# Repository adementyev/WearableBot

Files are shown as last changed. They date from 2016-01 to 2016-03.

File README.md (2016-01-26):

#Rovables Project 

#Motor Driver V2 (Main robot controller)
The robot controller board contains the necessary components to make functional robot. 
It has a brain of ATmega328p microcontroller, 6-Axis IMU and 2.4GHz wireless board
Also, it can take input from two encoders. 
A extension board can be placed on the top. 

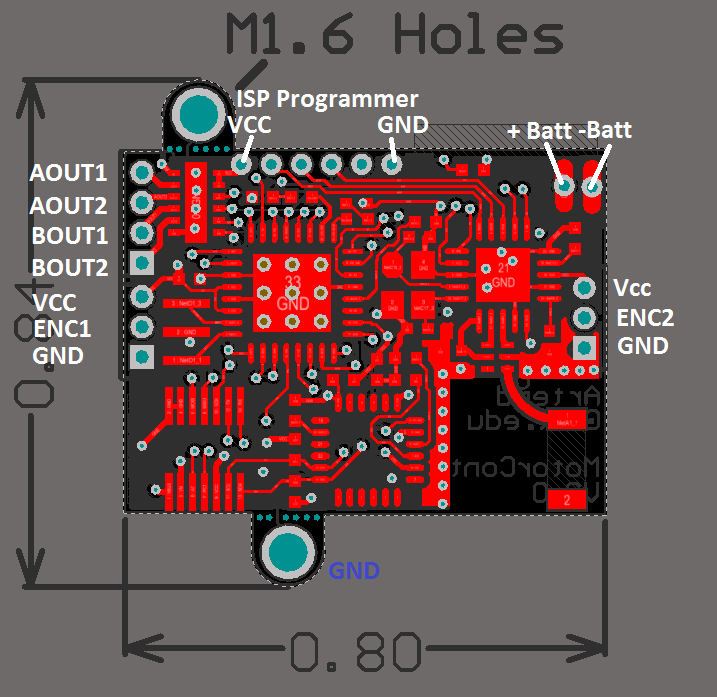
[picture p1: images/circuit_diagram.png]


##Programming the controller board 
The board needs AVRISPmkII programmer, and a special programming adapter. The programming connector can be just pressed fited into the holes. The power is not supplied by the programmer, so a seperate power supply will be needed. 
When programming choose Arduino Pro Mini (3.3V, 8MHz) w/ ATmega328 

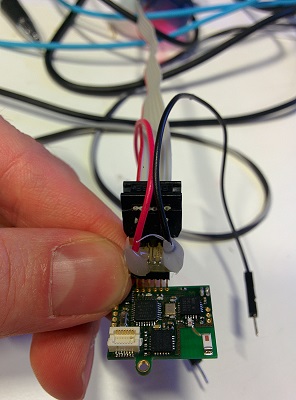
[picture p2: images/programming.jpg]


##Optical Encoders
The board can take two optical encoders. The onboard comparators will convert the analog signals into digital interrupts. Two digital to analog converters (DACs) can be used to set the threshold for comparator. It can be tricky to tune it. It is best done with two oscillascope probes. One on the analog output of optical sensor, and second on the comparator digital output. 

##Problems 
The packet loss is quite large (1 out of 20 ). I suspect it is because of the antenna. 

#Base station board 
Base station allows the robot to wirelessly talk to the computer. 
It is essentially Arduino Leonardo with special connector for a RF dongle. 
The ATMega32u4 processor allow fast USB communications to the computer

##Programming the controller board
The board has a Ardiono USB bootloader so it can be programmed as regular Arduino Leonardo. 

#Software
The current version of the software runs in OpenFrameworks. Tested on Xcode/MacBook Pro only C++ allows for faster 3D graphics, and faster response. The robot can be controlled remotely from the computer.

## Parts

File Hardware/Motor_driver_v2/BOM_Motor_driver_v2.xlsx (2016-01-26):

Comment | Description | Designator | digikey number | Footprint | LibRef | Quantity
ON_OFF_SWITCH | SPDT SMD Side Switch |  | 10 | SWTICH_SMD_SIDE | ON_OFF_SWITCH | 1
2.45 GHz Chip antenna | for Bluetooth | A1 | 712-1005-1-ND | 2450AT18A100E | 2.45 GHz Chip antenna | 1
2.45 GHz Bulan | for nRF8001 chip | B1 | 712-1574-1-ND | 2450BM14A0002 | 2.45 GHz Bulan | 1
100uF 6.3V | Polarised capacitor | C1 | 718-1920-1-ND | CAP1206 | Capacitor_pol | 1
0.1uF | SMD Cap 1206 | C3, C5, C6, C8 | 1276-1443-1-ND | 0402W | Capacitor | 4
10uF 16V | Polarised capacitor | C4 | 478-8654-1-ND | CAP0805 | Capacitor_pol | 1
10nF | SMD Cap 1206 | C7 | 587-3383-1-ND | 0402W | Capacitor | 1
2200pF | SMD Cap 1206 | C9 | 587-3383-1-ND | 0402W | Capacitor | 1
10uF 6.3V | Polarised capacitor | C10 | 478-9265-1-ND | 0805 TANTALUM | Capacitor_pol | 1
0.1uF | SMD Cap 1206 | C11, C12, C14 |  | 0603W | Capacitor | 3
33nF X7R, +/- 10% | SMD Cap 1206 | C13 | 399-4891-1-ND | 0402W | Capacitor | 1
6pF NPO, +/- 2% | SMD Cap 1206 | C15, C17 | 490-8223-1-ND | 0402W | Capacitor | 2
2200pF 5% | SMD Cap 1206 | C16 | 399-8957-1-ND | 0402W | Capacitor | 1
LED RED |  | L2 | LNJ247W82RACT-ND | 0402W
LED BLUE |  | L1 | LNJ947W8CRACT-ND | 0402W | LED | 2
8 MHz resonator | Build in caps | O1 | 490-1195-1-ND | Resonator SMD | Resonator SMD | 1
16 MHz Crystal Cl=8pF | For BLE use | O2 | 644-1169-1-ND | 2.5 x 2.0 crystal | 16 MHz Crystal Wireless | 1
MHDR1X3 | Header, 3-Pin | P1, P2 |  | MHDR1X3 | MHDR1X3 | 2
CONN HEADER 14POS 3MM SMD 0.5MM |  | P3 | H11701CT-ND | DF12 14Pos | CONN HEADER 14POS 3MM SMD 0.5MM | 1
MHDR1X4 | Header, 4-Pin | P4 |  | MHDR1X4 | MHDR1X4 | 1
6 pin smd 1.27mm female |  | P6 | ED90490-ND | 6pos 1.27mm | 6 pin smd 1.27mm female | 1
0 Ohm |  | R1 | 311-0.0GRCT-ND | 0603W | Resistor | 1
330 |  | R2, R3 | 311-330JRCT-ND | 0402W | Resistor | 2
4.7k |  | R4, R5, R6 | 311-4.7KJRCT-ND | 0402W | Resistor | 3
10k |  | R7 | 311-10.0KLRCT-ND | 0402W | Resistor | 1
22K 1% |  | R8 | P20.0KLCT-ND | 0402W | Resistor | 1
3.7V REG | DNP | U1 | 576-2770-1-ND | SOT-23-5 | MIC5205_VOLTAGE_REG | 1
MPU 6050 | Gyro / accelerometer combo | U2 |  | QFN24 | MPU_6500 | 1
ATmega328P-MUR | 8-bit AVR Microcontroller, 32KB Flash, 1KB EEPROM, 2KB SRAM, 32-pin MLF, Industrial Grade (-40°C to 85°C) | U3 | ATMEGA328P-MURCT-ND | 32M1-A_M | ATmega328P-MUR | 1
3.3 V REG | 150mA | U4 | 576-1259-1-ND | SOT-23-5 | MIC5205_VOLTAGE_REG | 1
DRV8835 | motor driver | U5 | 296-30391-1-ND | WSON-16 | DRV8835 | 1
MCP4725 | 12bit DAC | U6, U9 | MCP4725A0T-E/CHCT-ND | SOT23-6 | MCP4725 | 2
TS882IST | Rail-to-rail 1.1 V dual comparatpr | U7 | 497-13800-1-ND | MiniS08 | TS882IST | 1
nRF24L01+ | 2.4 GHz Radio | U8 | 1490-1033-1-ND | QFN20 | nRF24L01+ | 1

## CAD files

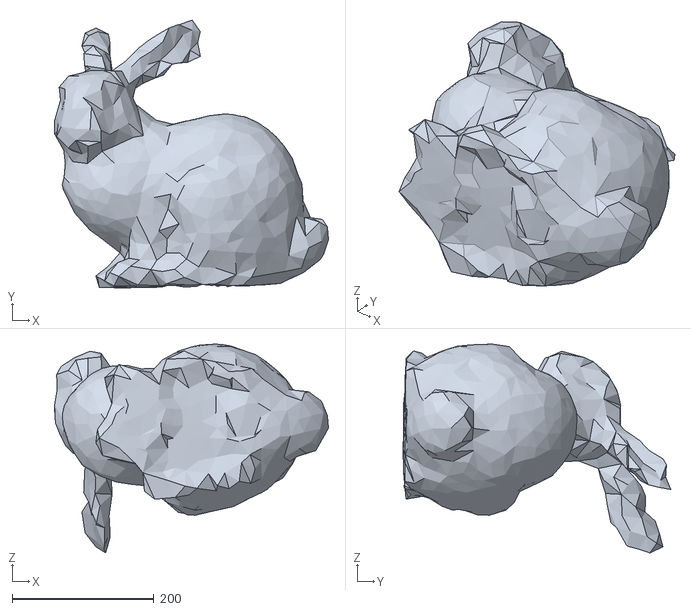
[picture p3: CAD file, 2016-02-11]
Software/onBodyNavigation_V2/bin/data/lofi-bunny_large.ply
386.4 x 377.6 x 294.6

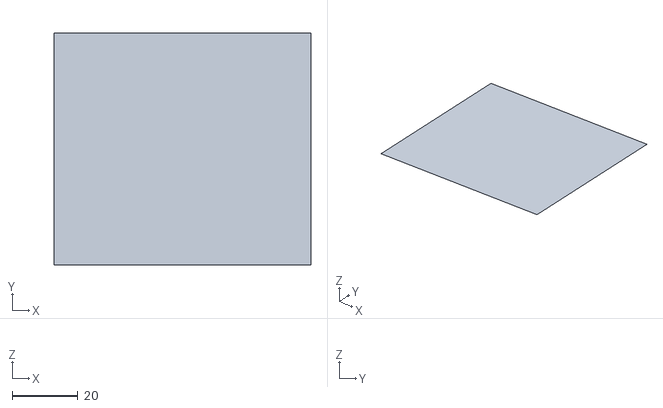
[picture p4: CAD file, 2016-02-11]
Software/onBodyNavigation_V2/bin/data/mesh_try2.ply
78.2 x 70.5 x 0

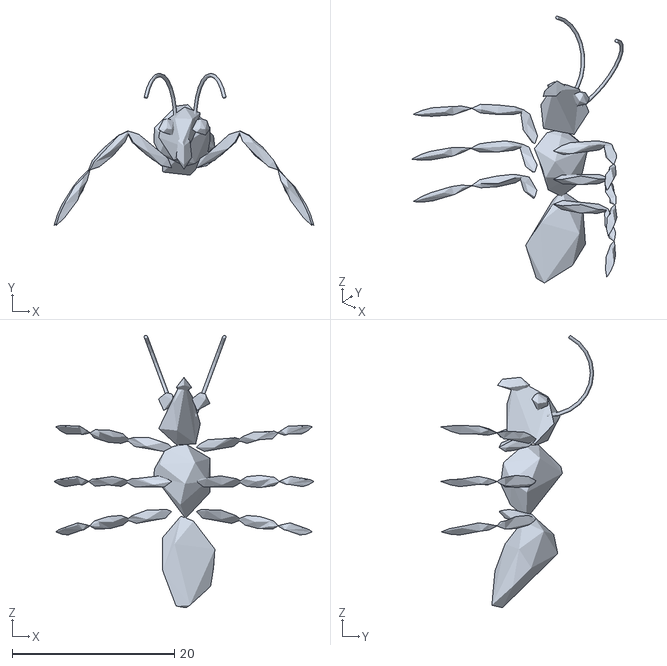
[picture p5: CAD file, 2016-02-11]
Software/onBodyNavigation_V2/bin/data/mesh_try1.ply
32.0 x 18.8 x 33.6

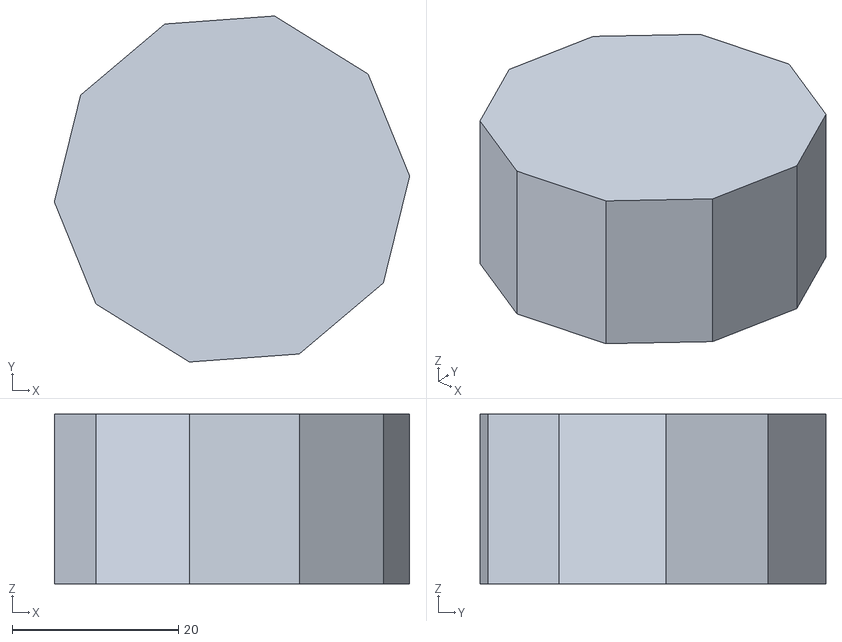
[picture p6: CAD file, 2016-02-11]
Software/onBodyNavigation_V2/bin/data/mesh_try4.ply
42.7 x 41.6 x 20.4

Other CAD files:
Software/onBodyNavigation_V2/bin/data/lofi-bunny.ply
Software/onBodyNavigation_V2/bin/data/mesh_try3.ply

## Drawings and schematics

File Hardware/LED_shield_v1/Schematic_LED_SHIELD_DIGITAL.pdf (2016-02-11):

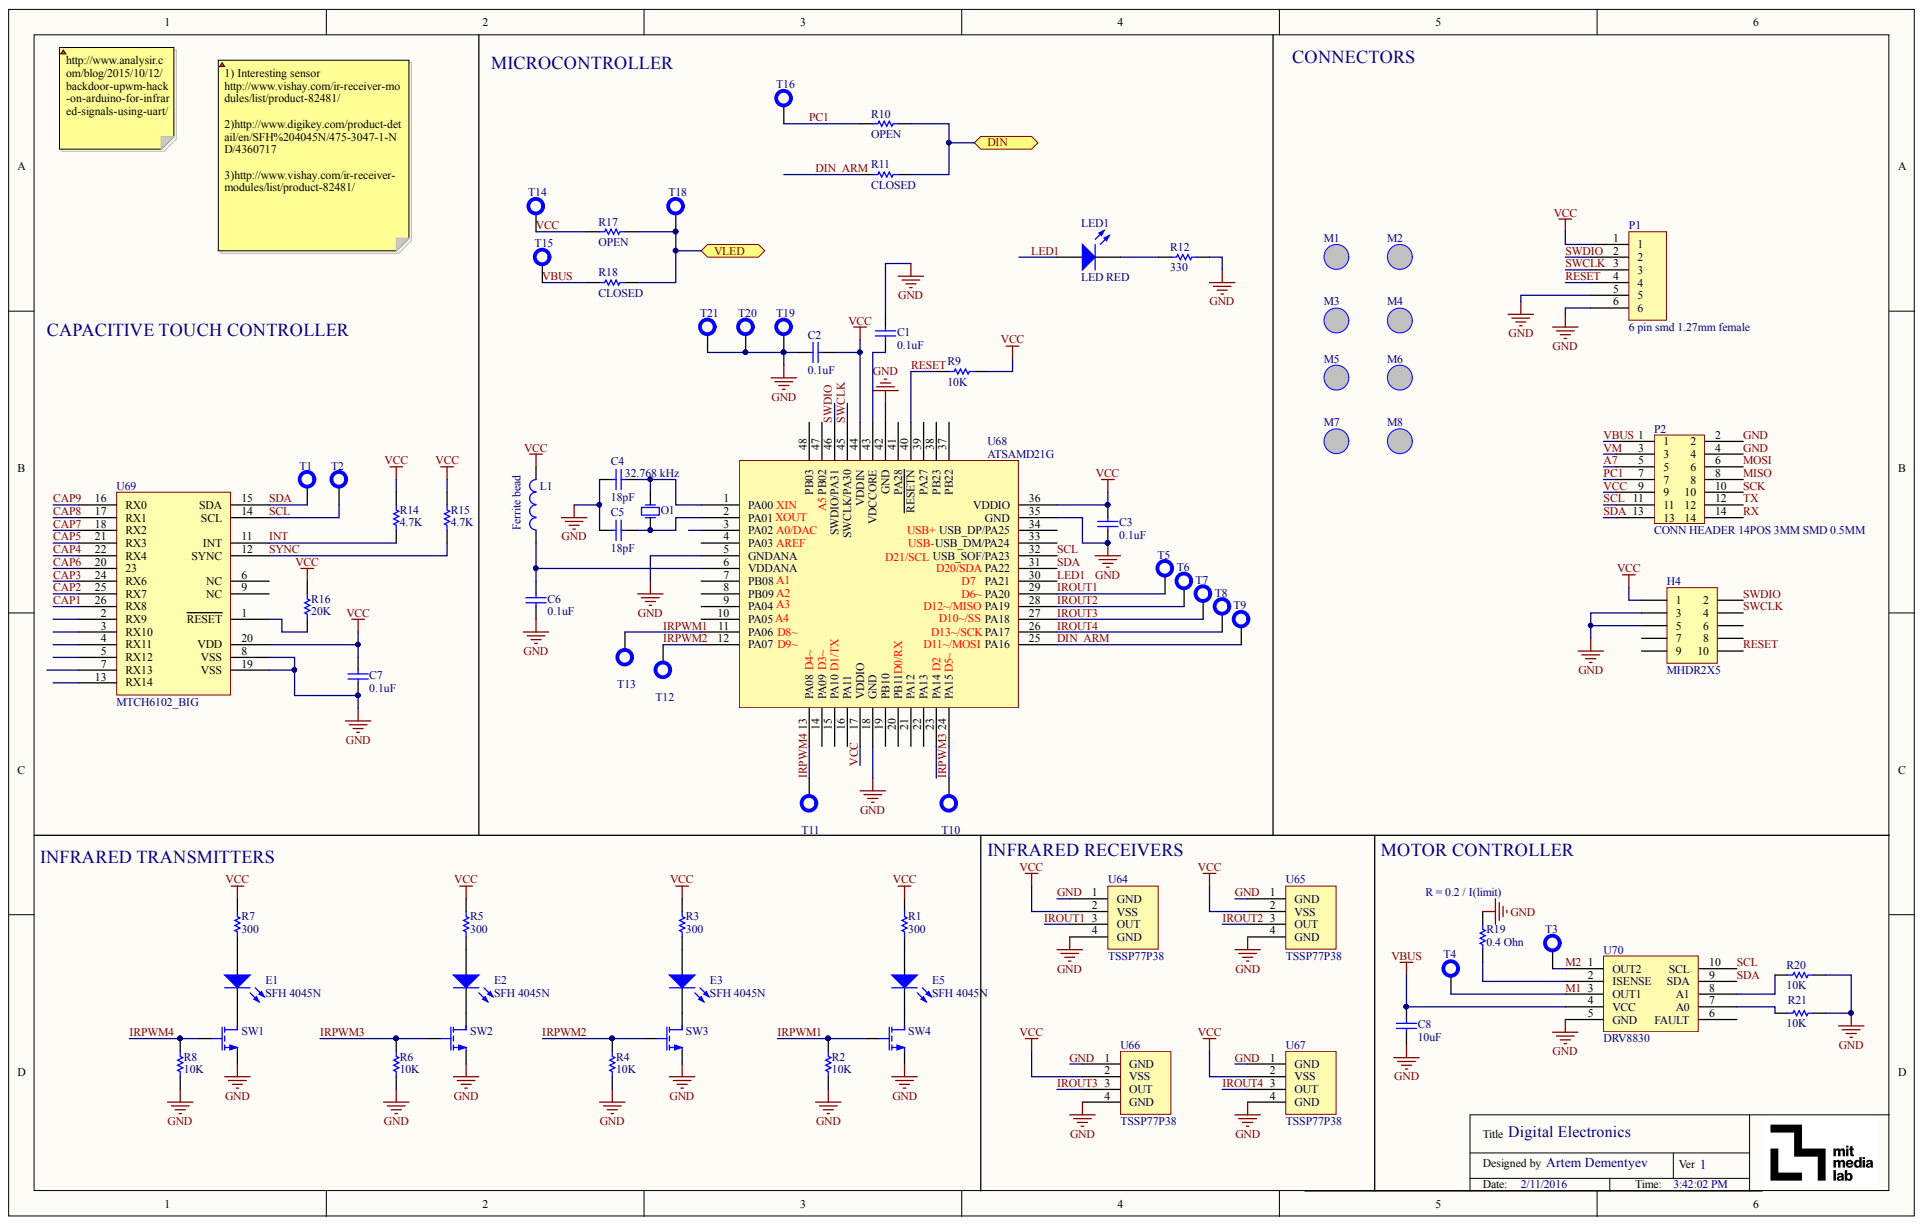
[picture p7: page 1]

http://www.analysir.c
om/blog/2015/10/12/
backdoor-upwm-hack
-on-arduino-for-infrar
ed-signals-using-uart/

1) Interesting sensor
http://www.vishay.com/ir-receiver-mo
dules/list/product-82481/

T16 CLOSED T14 T18 | VCC

2)http://www.digikey.com/product-det
ail/en/SFH%204045N/475-3047-1-N

3)http://www.vishay.com/ir-receiver-
modules/list/product-82481/

Designed by Artem Dementyev | Ver 1

Date: 2/11/2016 | Time: 3:42:02 PM

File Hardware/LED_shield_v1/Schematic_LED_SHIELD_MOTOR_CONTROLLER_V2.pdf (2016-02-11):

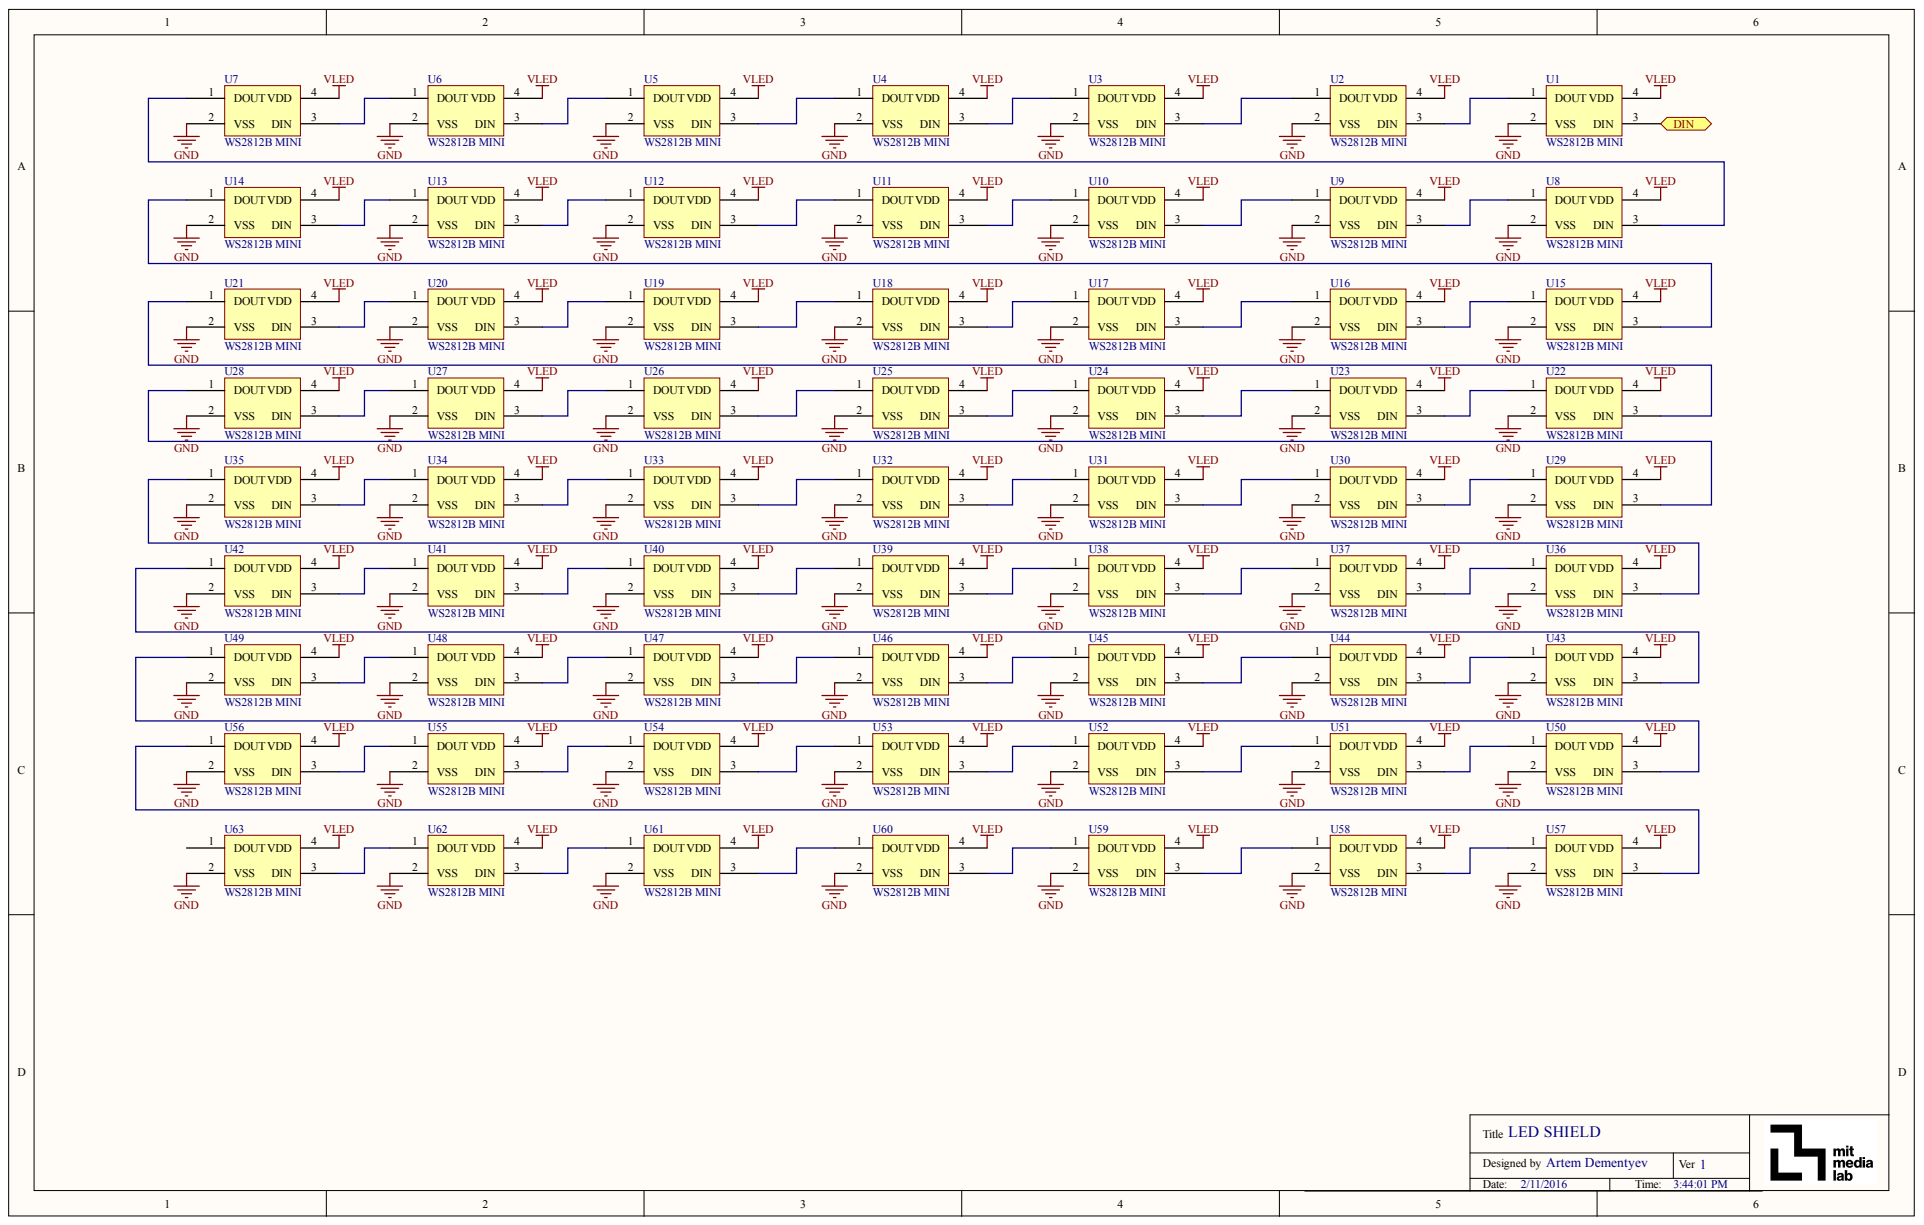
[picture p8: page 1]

Title LED SHIELD

Designed by Artem Dementyev | Ver 1

Date: 2/11/2016 | Time: 3:44:01 PM

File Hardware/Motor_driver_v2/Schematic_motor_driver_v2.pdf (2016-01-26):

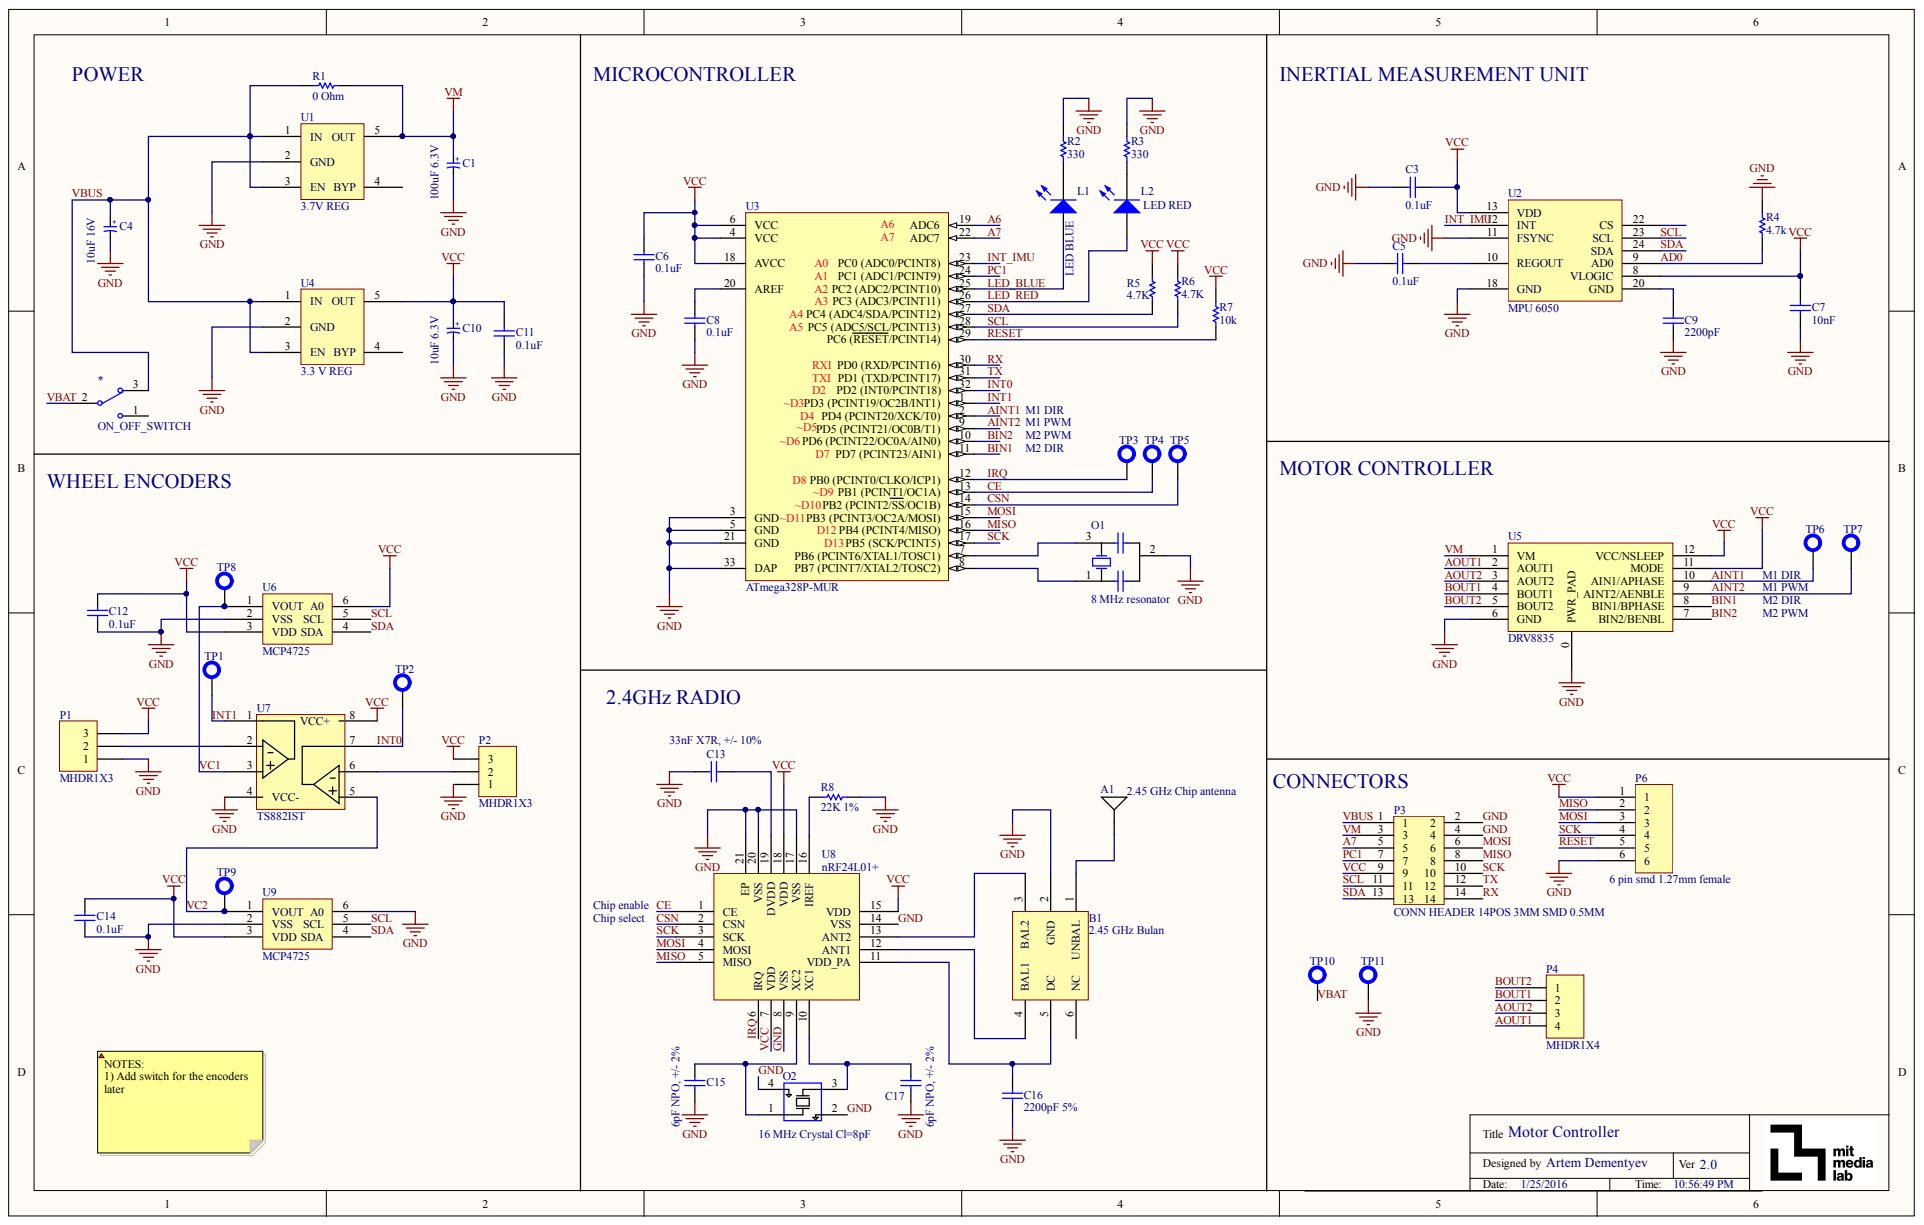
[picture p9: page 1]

IREF 16 VSS 17 VDD 18 DVDD 19 VSS 20 V

2 | 9 MCP4725 VSS V D D A

tch for the encoder

Ti t l e Mo t or Co n tro l ler

Des igned by A r tem Demen t yev | 2 . 0 Ver

Date: 1/25/2016 | Ti me: 10:56:49 PM

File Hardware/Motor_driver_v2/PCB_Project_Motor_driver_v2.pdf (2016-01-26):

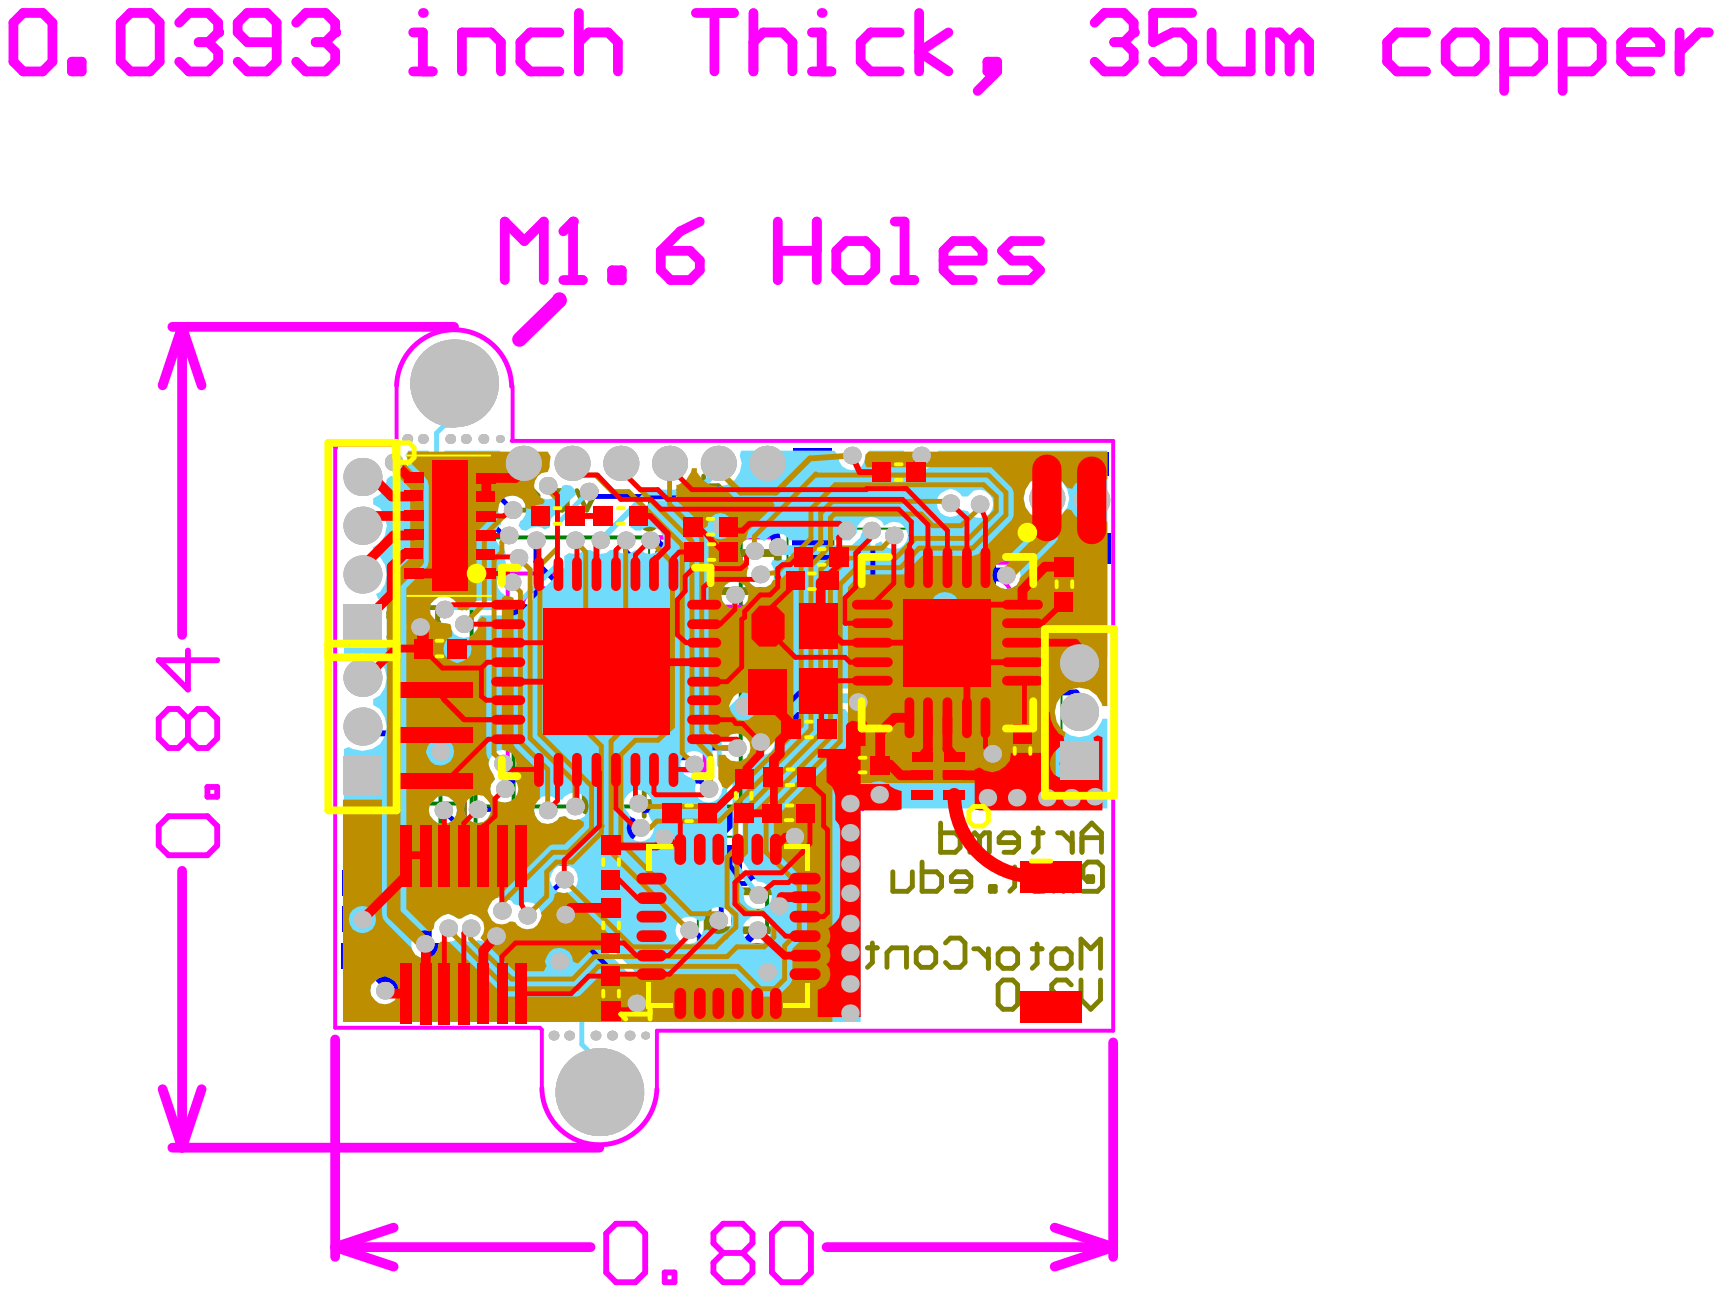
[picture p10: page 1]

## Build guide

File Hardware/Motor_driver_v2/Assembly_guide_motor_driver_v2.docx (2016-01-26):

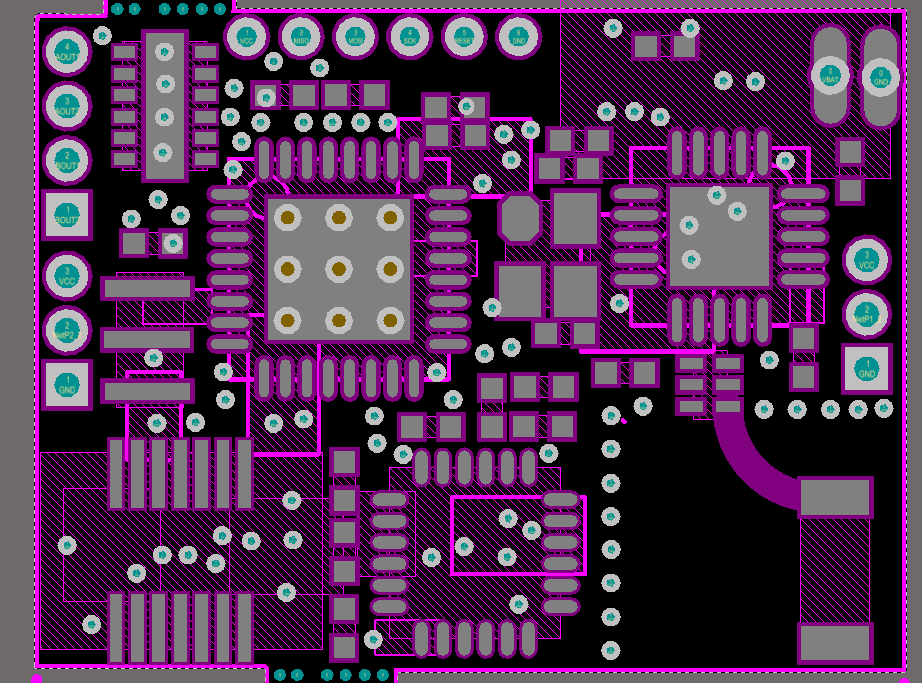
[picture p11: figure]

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
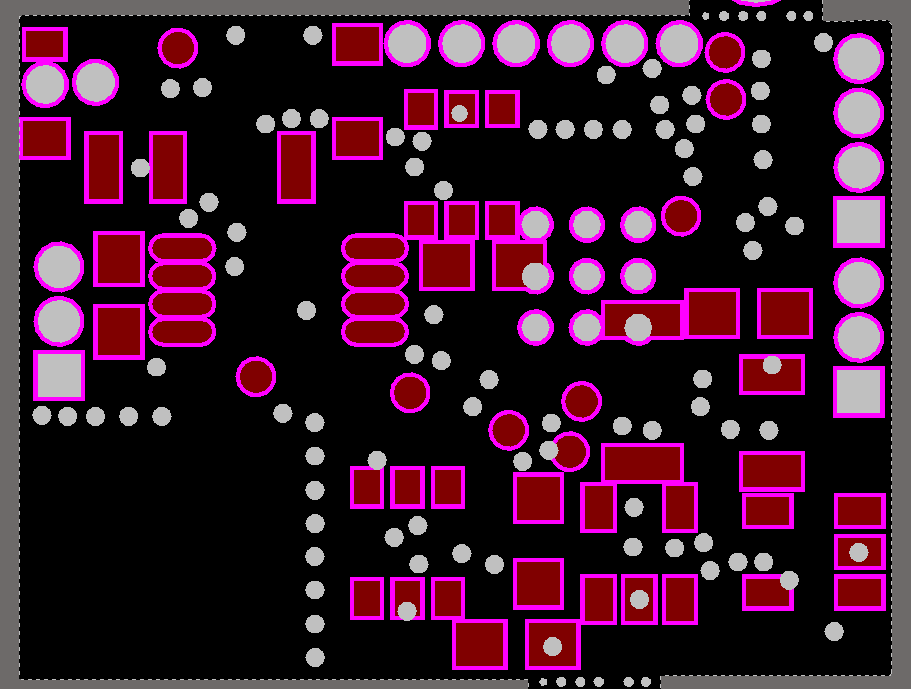
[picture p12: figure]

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
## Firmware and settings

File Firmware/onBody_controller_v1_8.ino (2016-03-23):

//Created by Artem Dementyev on Feb 23, 2016
//TODO fix serial crashes

//Added the PID controller to this version

//REMEMBER to set I2C implementation to 2CDEV_ARDUINO_WIRE

//FIFO data rate is determined by MPU6050_6Axis_MotionApps20.h line 305
//last line 0x13 seems to be working ok, this drops data rate to 10 Hz
//now I want to increase it more so lets say 20 Hz

#include <SPI.h>
#include <RH_NRF24.h>
#include <RHReliableDatagram.h>
#include <Wire.h>
#include <Adafruit_MCP4725.h>
#include <avr/io.h>
#include <avr/interrupt.h>   
#include "MPU6050_6Axis_MotionApps20.h"
#include "I2Cdev.h"
#include <PID_v1.h>
#include <RovablesARMMotor.h>

//Define PID
//Kd is at least 20 times bigger than Kp in my case
#define Kp .7 //0.1 before 
#define Kd 0.1
#define Ki 0 
//Tune Kp first? 

//.1/.5/.01

//Define MotorSpeeds
#define rightMaxSpeed 200 // max speed of the robot
#define leftMaxSpeed 200 // max speed of the robot
#define rightBaseSpeed 100 
#define leftBaseSpeed 100  

//Define Pins
#define  LED_BLUE A2
#define  LED_RED  A3 
#define  CE       9  
#define  CSN      10 
#define  M1_DIR   4 
#define  M1_PWM   5 
#define  M2_PWM   6 
#define  M2_DIR   7 
#define  INT_IMU  A0
#define  PC1_PIN  A1
//#define  INT0_PIN     2
//#define  INT1_PIN     3  

#define CLIENT_ADDRESS 1
#define SERVER_ADDRESS 2

#define DAC_LEFT_ADDRESS  0x60
#define DAC_RIGHT_ADDRESS  0x61

RH_NRF24 nrf24(CE, CSN);// CE, CSN pins
RHReliableDatagram manager(nrf24, CLIENT_ADDRESS);
Adafruit_MCP4725 dacLeft;
Adafruit_MCP4725 dacRight;
MPU6050 mpu;
RovablesMotor motor(0xE0);    //Wire library handle 0xE0 as 0xC0 (true value from datasheet)

uint8_t data[] = "And hello back to you1223";
// Dont put this on the stack:
uint8_t buf[RH_NRF24_MAX_MESSAGE_LEN];
    
byte counter  = 0; 

String inputString = "";         // a string to hold incoming data
boolean stringComplete = false;  // whether the string is complete
int encoder1Counter = 0; 
int encoder2Counter = 0;

uint8_t devStatus;      // return status after each device operation (0 = success, !0 = error)
uint8_t mpuIntStatus;   // holds actual interrupt status byte from MPU
uint16_t packetSize; 
uint8_t fifoBuffer[64]; // FIFO storage buffer
uint16_t fifoCount;     // count of all bytes currently in FIFO

uint8_t distanceToTravel = 0;
float yaw =0.0; 

boolean remoteNavigation = false; 
boolean timer1int = false;

Quaternion q;           // [w, x, y, z]         quaternion container
//double PID_input, PID_output, PID_setPoint; 
//PID myPID(&PID_input, &PID_output, &PID_setPoint,2,5,1,DIRECT);
//PID myPID(&PID_input, &PID_output, &PID_setPoint,.3,0.001,0.001,DIRECT);
uint8_t MOTOR_BASE_VALUE = 60;
uint8_t sumEncoder1 = 0; 

int lastError = 0; 
int PID_setPoint = 0;
int integral = 0;

void setup()
{
  pinMode(LED_RED, OUTPUT);     
  pinMode(LED_BLUE,OUTPUT);
  pinMode(M1_DIR, OUTPUT); 
  pinMode(M1_PWM, OUTPUT); 
  pinMode(M2_PWM, OUTPUT); 
  pinMode(M2_DIR, OUTPUT); 
  pinMode(INT_IMU, INPUT);
  pinMode(PC1_PIN, INPUT);
  
  
  dacLeft.begin(DAC_LEFT_ADDRESS);
  dacRight.begin(DAC_RIGHT_ADDRESS);
  dacLeft.setVoltage(650,false); //950 // 30
  dacRight.setVoltage(650,false); //4094 is max
  
  
 // Wire.begin();
//  TWBR = 24; // 400kHz I2C clock (200kHz if CPU is 8MHz).
  TWBR = 2;  //This sets the clock to 400kHz for I2C ((8*10^6) / (16+2*(2)*1))/1000
  mpu.initialize();
  uint8_t devStatus = mpu.dmpInitialize();
  
    // supply your own gyro offsets here, scaled for min sensitivity
  mpu.setXGyroOffset(220);
  mpu.setYGyroOffset(76);
  mpu.setZGyroOffset(-85);
  mpu.setZAccelOffset(1788); // 1688 factory default for my test chip
  
  if (devStatus ==0 ) { 
      mpu.setDMPEnabled(true);
      mpuIntStatus = mpu.getIntStatus();
      packetSize = mpu.dmpGetFIFOPacketSize();
  }
  else { 
    digitalWrite(LED_RED, HIGH);
  }



/*
  if (!nrf24.init())
    digitalWrite(LED_RED,HIGH);
  // Defaults after init are 2.402 GHz (channel 2), 2Mbps, 0dBm
  if (!nrf24.setChannel(1))
    digitalWrite(LED_RED,HIGH);
  if (!nrf24.setRF(RH_NRF24::DataRate2Mbps, RH_NRF24::TransmitPower0dBm))
    digitalWrite(LED_RED,HIGH);
    */
    
  if (!manager.init())
      digitalWrite(LED_RED,HIGH);
      
//  if (!nrf24.setRF(RH_NRF24::DataRate1Mbps, RH_NRF24::TransmitPower0dBm))
//    digitalWrite(LED_RED,HIGH);
    //  Serial.println("init failed");
  // Defaults after init are 2.402 GHz (channel 2), 2Mbps, 0dBm
 
  //  analogWrite(M1_PWM, 100); 
  //  analogWrite(M2_PWM, 100); 
   manager.setTimeout(random(5,100));
   setupExternalInterrupts();
   setupTimer1();
  // setupTimer2();
//   OCR0A = 0xAF;
//  TIMSK0 |= _BV(OCIE0A);
   
   sei(); //enable interrupts
}

//-----------------INTERRUPT SERVICE ROUTINES----------------
ISR (INT0_vect)
{
  encoder1Counter++;   
  sumEncoder1++;
  //enable timer 2 
  //disable ISR0
  
  
   //----ENABLE TIMER 2--------
    OCR2A = 249; //2 ms delay

    TCCR2A |= (1 << WGM21);
    // Set to CTC Mode

    TIMSK2 |= (1 << OCIE2A);
    //Set interrupt on compare match

    TCCR2B |= (1 << CS22);
    // set prescaler to 64 and starts PWM
    
  //----DISABLE INT0 ---------
  EIMSK |= (0 << INT0);     
  
  
}

ISR (INT1_vect)
{
 encoder2Counter++;  
 //enable timer 2
 //disable ISR 1
}

ISR (TIMER1_COMPA_vect)  // timer1 overflow interrupt
{
    //event to be exicuted every 4ms here
    data[3] = encoder1Counter; 
    data[4] = encoder2Counter;
    encoder1Counter=0; 
    encoder2Counter=0;
    timer1int = true;
   // PINC = (1<<2);
  //  PORTC^= (1<<2) ;
}

ISR (TIMER2_COMPA_vect) // timer2 overflow interrupt
{ 
 //disable timer 2
 //enable ISR0
 
     //---DISABLE TIMER 2-------
    TCCR2B |= (0 << CS22);
    
    //----ENABLE INT 0--------
    EIMSK |= (1 << INT0);     // Turns on INT0
}

ISR (TIMER0_COMPA_vect)  // timer0 overflow interrupt
{
    //Used to PWM motors already :(, So can't be used. 
}


void loop()
{
  
  //-----------GET MPU DATA--------------
   mpuIntStatus = mpu.getIntStatus();
   fifoCount = mpu.getFIFOCount();
  
 if ((mpuIntStatus & 0x10) || fifoCount == 1024) {
      // reset so we can continue cleanly
      mpu.resetFIFO();
      
  // otherwise, check for DMP data ready interrupt (this should happen frequently)
  } else if (mpuIntStatus & 0x02) {
      // wait for correct available data length, should be a VERY short wait
      while (fifoCount < packetSize) fifoCount = mpu.getFIFOCount();

      // read a packet from FIFO
      mpu.getFIFOBytes(fifoBuffer, packetSize);
      mpu.dmpGetQuaternion(&q, fifoBuffer);
    //  digitalWrite(LED_BLUE, !digitalRead(LED_BLUE));
      
      if(remoteNavigation==true) { 
        //digitalWrite(LED_RED, HIGH);
        delay(1);
        doPIDstuff();
        if (sumEncoder1 > distanceToTravel) { 
         // remoteNavigation = false;
        //  sumEncoder1 = 0;
        }//end if
      }//end if 

    }//end else if
  
    


//-----------CHECK TIMER 1--------------
  if (timer1int == true && remoteNavigation==false) { 
    timer1int=false;
    counter++;
   if (counter>243)  {counter=0;}
    data[1] = counter; //counter
    data[2] = manager.retransmissions();
    data[3] = encoder1Counter; 
    data[4] = encoder2Counter;
    data[5] = fifoBuffer[1];
    data[6] = fifoBuffer[0]; 
    data[7] = fifoBuffer[5];
    data[8] = fifoBuffer[4]; 
    data[9] = fifoBuffer[9]; 
    data[10] =fifoBuffer[8];
    data[11] =fifoBuffer[13]; 
    data[12] =fifoBuffer[12];
    
 //-----------SEND THE DATA TO COMPUTER--------------      
    if (manager.sendtoWait(data, sizeof(data), SERVER_ADDRESS))
    {  
     // digitalWrite(INT0, HIGH);
      // Now wait for a reply from the server
      uint8_t len = sizeof(buf);
      uint8_t from;   
      if (manager.recvfromAckTimeout(buf, &len, 100, &from))
      {     
          switch (buf[0]) {
            //do nothing
            case 0x01:
              break; 
            //Control the motor
            case 0x02: 
              analogWrite(M1_PWM, buf[1]);
              analogWrite(M2_PWM, buf[2]);
              digitalWrite(M1_DIR, buf[3]); 
              digitalWrite(M2_DIR, buf[4]);
              break;     
            //Blink the blue LED
            case 0x03:
              digitalWrite(LED_BLUE, !digitalRead(LED_BLUE));
              break;    
            //Set DACs to a specific voltage 
            case 0x04: 
              dacLeft.setVoltage(buf[1]*16,false); //950 // 30
              dacRight.setVoltage(buf[2]*16,false); //4094 is max
              break;    
            //Go forward with PID control
            case 0x05: 
              digitalWrite(LED_RED, !digitalRead(LED_RED));
              digitalWrite(M1_DIR, 1);
              digitalWrite(M2_DIR, 0);
              updateYaw();
              //PID_setPoint = (double)(yaw*(180/3.14));          
              distanceToTravel = buf[1];
              sumEncoder1=0;
              remoteNavigation = true;
              break;
            case 0x06: 
              break;           
            case 0xAA: 
              digitalWrite(LED_RED,HIGH);
              motor.driveForward(buf[1]);
              break;
            case 0xAB: 
              digitalWrite(LED_RED,LOW);
              motor.brake(); 
              break;
          }//end switch
      //  Serial.print("got reply from : 0x");
      //  Serial.print(from, HEX);
      //  Serial.print(": ");
      //  Serial.println((char*)buf);      
      }
      else
      {
      //  Serial.println("No reply, is nrf24_reliable_datagram_server running?");
      }
     // digitalWrite(INT0, LOW);
      
    }
    else {
  //        digitalWrite(LED_RED, !digitalRead(LED_RED));
    }
  }//end timer1Int
  
    //Serial.println("sendtoWait failed");
  //  digitalWrite(LED_RED, !digitalRead(LED_RED));
 // delay(100);
  
}

void setupExternalInterrupts() { 
    DDRD &= ~(1 << DDD2);     // Clear the PD2 pin
    DDRD &= ~(1 << DDD3);     // Clear the PD3 pin
    // PD2 (PCINT0 pin) is now an input
    
   // PORTD |= (1 << PORTD2);    // turn On the Pull-up
   // PORTD |= (1 << PORTD3);    // turn On the Pull-up
    // PD2 is now an input with pull-up enabled
    
    // set INT0 to trigger on RISING EDGE
    EICRA |= (1 << ISC00);    
    EICRA |= (1 << ISC01);    // set INT0 to trigger on ANY logic change
    EIMSK |= (1 << INT0);     // Turns on INT0
    
    // set INT1 to trigger on RISING EDGE
    EICRA |= (1 << ISC10);    // set INT1 to trigger on ANY logic change
    EICRA |= (1 << ISC11);    // set INT1 to trigger on ANY logic change
    EIMSK |= (1 << INT1);     // Turns on INT1
  //  sei();                    // turn on interrupts
}

void setupTimer1() { 
  TCCR1A = 0;// set entire TCCR1A register to 0
  TCCR1B = 0;// same for TCCR1B
  TCNT1  = 0;//initialize counter value to 0
  // set compare match register for 1hz increments
//  OCR1A = 7812;// = (16*10^6) / (1*1024) - 1 (must be <65536)
  OCR1A = 780;// = (8*10^6) / (10*1024) - 1 (must be <65536)
  // turn on CTC mode
  TCCR1B |= (1 << WGM12);
  // Set CS12 and CS10 bits for 1024 prescaler
  TCCR1B |= (1 << CS12) | (1 << CS10);  
  // enable timer compare interrupt
  TIMSK1 |= (1 << OCIE1A);
}


void setupTimer2() { 
      OCR2A = 200;

    TCCR2A |= (1 << WGM21);
    // Set to CTC Mode

    TIMSK2 |= (1 << OCIE2A);
    //Set interrupt on compare match

    TCCR2B |= (1 << CS20);
    TCCR2B |= (1 << CS21);
    TCCR2B |= (1 << CS22);
    // set prescaler to 64 and starts PWM
}

void computeYawPitchRoll() { 
     //Takes about 73us to compute on 16MHz clock, so about 140 us on 8MHz clock 
    float q[4];
    float w,x,y,z;
    float roll,pitch,yaw;
    
    q[0] = ((fifoBuffer[1]<<8) + fifoBuffer[0]) / 16384.0f;
    q[1] = ((fifoBuffer[5]<<8) + fifoBuffer[4]) / 16384.0f;
    q[2] = ((fifoBuffer[8]<<8) + fifoBuffer[9]) / 16384.0f;
    q[3] = ((fifoBuffer[12]<<8) + fifoBuffer[13]) / 16384.0f;
    for (int i = 0; i < 4; i++) {
        if (q[i] >= 2) q[i] = -4 + q[i];
    }
    w = q[0];
    x = q[1];
    y = q[2];
    z = q[3];
    
    roll = atan2((float) (2.0*(y*z + w*x)), w*w - x*x - y*y + z*z);
    pitch = (float) (-1.0 * asin((float) (-2.0*(x*z - w*y))));
    yaw = atan2((float) (2.0*(x*y + w*z)), w*w + x*x - y*y - z*z);
}

void updateYaw() { 
    float q[4];
    float w,x,y,z;
    
    q[0] = ((fifoBuffer[0]<<8) + fifoBuffer[1]) / 16384.0f;
    q[1] = ((fifoBuffer[4]<<8) + fifoBuffer[5]) / 16384.0f;
    q[2] = ((fifoBuffer[8]<<8) + fifoBuffer[9]) / 16384.0f;
    q[3] = ((fifoBuffer[12]<<8) + fifoBuffer[13]) / 16384.0f;
    for (int i = 0; i < 4; i++) {
        if (q[i] >= 2) q[i] = -4 + q[i];
    }
    w = q[0];
    x = q[1];
    y = q[2];
    z = q[3];
    
   // roll = atan2((float) (2.0*(y*z + w*x)), w*w - x*x - y*y + z*z);
   // pitch = (float) (-1.0 * asin((float) (-2.0*(x*z - w*y))));
    yaw = atan2((float) (2.0*(x*y + w*z)), w*w + x*x - y*y - z*z);
} 

void doPIDstuff() { 
  updateYaw();
  int currentYaw = (int)(yaw*(180/3.14));
  int error = currentYaw - 50;
  int motorSpeed = Kp * error + Kd * (error-lastError) + integral * error * Ki; 
  lastError = error; 
  integral = integral + error;
 // myPID.Compute(); 
 
  int rightMotorSpeed = rightBaseSpeed + motorSpeed;
  int leftMotorSpeed = leftBaseSpeed - motorSpeed;
  
  if (rightMotorSpeed > rightMaxSpeed ) rightMotorSpeed = rightMaxSpeed; // prevent the motor from going beyond max speed
  if (leftMotorSpeed > leftMaxSpeed ) leftMotorSpeed = leftMaxSpeed; // prevent the motor from going beyond max speed
  if (rightMotorSpeed < 0) rightMotorSpeed = 0; // keep the motor speed positive
  if (leftMotorSpeed < 0) leftMotorSpeed = 0; // keep the motor speed positive
  
  analogWrite(M1_PWM, rightMotorSpeed);
  analogWrite(M2_PWM, leftMotorSpeed);
  
  if (error < 5) { 
  digitalWrite(LED_RED, HIGH); 
  }
  else {digitalWrite(LED_RED, LOW);}
  //SPI.transfer((byte)motorSpeed);
  //SPI.transfer((byte)rightMotorSpeed);
  //SPI.transfer((byte)leftMotorSpeed); 
  
}

void initializePID() {
  updateYaw(); 
  PID_setPoint = (int)(yaw*(180/3.14));
  //myPID.SetMode(AUTOMATIC);
  //myPID.SetSampleTime(2);
  sumEncoder1=0;
  integral = 0; 
}

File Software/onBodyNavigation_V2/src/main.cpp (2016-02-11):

//
//  main.cpp
//  onBodyNavigation_V2
//
//  Created by Artem Dementyev  artemd@mit.edu on 2/10/16.
//
//

#include "ofMain.h"
#include "ofApp.h"

//========================================================================
int main( ){
	ofSetupOpenGL(1024,768,OF_WINDOW);			// <-------- setup the GL context

	// this kicks off the running of my app
	// can be OF_WINDOW or OF_FULLSCREEN
	// pass in width and height too:
	ofRunApp(new ofApp());

}

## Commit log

2016-01-26 added hardware design files
    [BOM_Motor_driver_v2.xlsx, PCB_motor_driver_v2.PcbDoc, Project_Motor_driver_v2.PrjPcb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]
2016-02-11 added multiple robot support
    [lofi-bunny.ply, lofi-bunny_large.ply, mesh_try1.ply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]
2016-02-11 led shied added
    [LED_SHIELD_MOTOR_CONTROLLER_V2.PrjPcb, PCB_LED_SHIELD_MOTOR_CONTROLLER_V2.PcbDoc, Schematic_LED_SHIELD_DIGITAL.SchDoc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]
2016-03-23 added initial PID control
